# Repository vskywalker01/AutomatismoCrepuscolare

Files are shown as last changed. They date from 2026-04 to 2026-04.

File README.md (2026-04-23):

# Solar-Switcher
This repository contains *source code* and *PCB design* for an automatic load switcher that controls high power consumption devices in base of the energy that a photovoltaic system can currently generate.

## How it works 
The switcher contains four different relays controlled by an Arduino Pro Mini that collects periodically samples from a photo-resistor aligned with the panels and converts them into an estimated power (the power that the inverter should be capable to generate at the time). 
<p align="center">
schematic
</p>

In base of a fixed priority order, the controller turns on and off the relays so that the overall consumptions fits into the estimated power.

## Software 
The software provide a simple user interface controllable by only three buttons (PLUS, MINUS and CONTROL) which contains a general visualization of the relays with dedicated pages for their details and a settings menu, for editing the options in real time. 

> [!NOTE]
> All the settings are automatically saved into the internal EEPROM of the Arduino microcontroller. 

> [!IMPORTANT]
> Currently, only Italian is supported as display language (English support may follow in next updates).

### Sensor conversion and calibration 
The photoresistor used for sampling the light intensity is used for estimating the power that the inverter system can generate on the fly. For this purpose, the analog pin A0 reads constantly the raw values and converts them using a power function defined as 

<h2 align="center">$(\frac{raw - \gamma}{\alpha})^\beta$</h2> 

The three parameters should be tuned by the user in the settings menu in order to assure that the power estimated follows the real one provided by the inverter. 

A good way to do that is to collect known points between *light* value and *power* consumption from the display and tune the parameters on Geogebra so that the curve pass near them. 

<p align="center">

</p>

In my case, for example, knowing that a pump consumes 2kW and a boiler 1.2kW, i obtained that the inverter can handle:
- **pump and boiler** (3,2kW) when the light value is greater or equal to *848*
- **pump until** (2kW) the light value is greater or equal to *800*

### Relay priority system 
The four relays are organined in a fixed priority order where the first one has the highest priority and the last one has the lowest priority. 

Using the power function, the solar switcher tries to turn on the highest amount of relays in order to fit into the estimated power obtained. This means that, as long as a relay with higher priority is turned on, the relays with lower priority will have less available energy. 

> [!NOTE]
> The user can choose to exlude a certain relay from the priority order in the settings using a mask that keeps it deactivated. 

### Source code 
The folder [*software*](software/) folder contains the commented source code of the Solar switcher ready to be flashed to the arduino board. A simple makefile downloads the required libraries, compiles the program and flash the microcontroller automatically using `arduino-cli`:

```
make run PORT=/dev/ttyUSB0 
```

## Hardware 
The folder [*pcb*](pcb/) contains the Kicad project, the [schematic](pcb/pdf/schematic.pdf),the specular [copper layer](pcb/pdf/output.pdf) ready for the press-n-peel and the [silkscreen](pcb/pdf/board.pdf). 

The required components are shown in the following table. 

| Name  | Quantity |
| --- | -- |
| Arduino Pro mini | x1 |
| LCD Display 16x2 | x1 |
| Button | x3 |
| Relay 12 to 24V | x4 |
| 74LS595 | x1 | 
| LM7805 | x1 | 
| BC237 | x4 |
| 1k Ohm resistor | x8 | 
| 10k Ohm resistor | x1 | 
| 510 Ohm resistor | x4 | 
| 10k Ohm trimmer | x1 |
| 2.2k trimmer | x1 | 
| LED | x4 |
| PC817 | x4 | 
| 1N4148 | x4 | 
| 100nf capacitor | x4 | 
| 200mf capacitor | x1 |

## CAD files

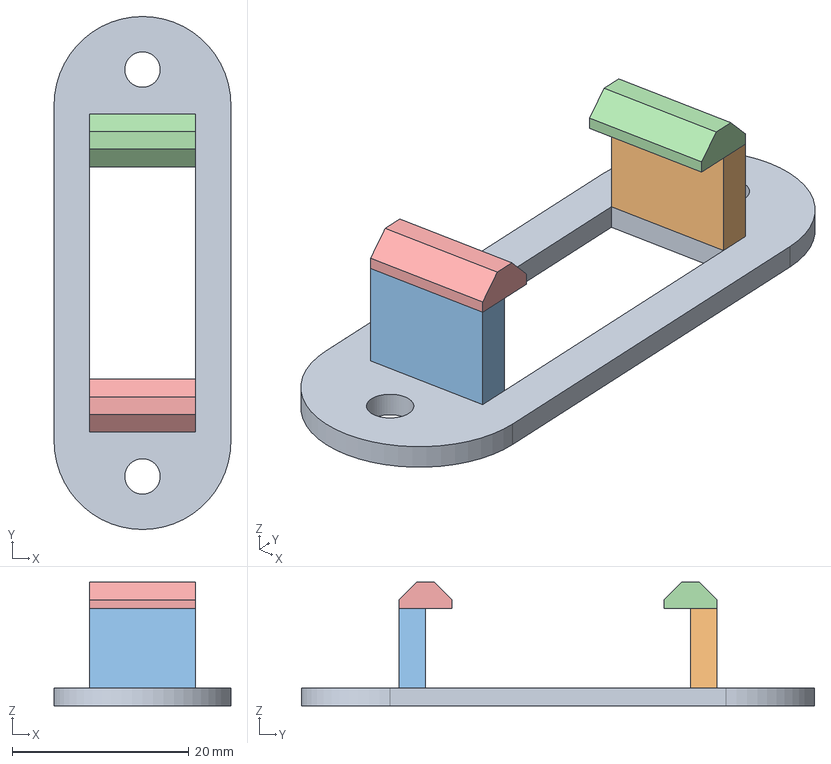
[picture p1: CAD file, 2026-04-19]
3D/button_mask.FCStd
20.0 x 58.0 x 14.0 mm

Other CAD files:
3D/STL/button_mask.stl

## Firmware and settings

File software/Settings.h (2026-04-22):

//Settings class definition 

#ifndef __SETTINGS_H__
#define __SETTINGS_H__

#include "Arduino.h"
#include <EEPROM.h>

/* This class is used for maintaining and storing settings of the program in the EEPROM internal memory. It defines a settings struct and methods to automatically save and load the information. 
 * To check if the data stored in the EEPROM are valid, a simple checksum is estimated and compared with the one stored in the memory. 
*/

#define DEFAULT_POWER       0
#define LOADS_NUMBER        4
#define DEFAULT_TIMEROFF    10
#define DEFAULT_TIMERON     10
#define DEFAULT_BUZZER      true 

#define DEFAULT_ALPHA       966 
#define DEFAULT_BETA        9.6 
#define DEFAULT_GAMMA       0

#define MAX_SETTINGS_BOUND  65536

using namespace std;

//SettingsValues is a struct used for containing the data to save/edit/load 
typedef struct SettingsValues{
    uint32_t checksum;                      //checksum used for verify the data 
    unsigned int powers[LOADS_NUMBER];      //power values for all relays 
    bool masks[LOADS_NUMBER];               //boolean masks for all relays 

    unsigned int defaultTimerOff;           //timer off value 
    unsigned int defaultTimerOn;            //timer on value 

    float alpha;                            //power estimation coefficients. 
    float beta; 
    float gamma;
} SettingsValues;

class Settings {
    private: 
    SettingsValues values;
    public:
    Settings();
    
    //loadDefault() loads default value sin the settings struct 
    void loadDefault();

    //load saved() loads the struct data from the given memory address and check if they are valid:
    //  address -> EEPROM addess of the saved data 
    //returns true if the loaded data is valid or false otherwise (default data is automatically loaded)
    //
    bool loadSaved(unsigned int address);
    
    //store() estimates the checksum and saved the fata from the settings struct to the given memory address 
    //  address -> EEPROM address where store the data 
    void store(unsigned int address);

    //Setter pf the various settings
    void setPower(unsigned int load, unsigned int value);
    void setTimerOn(unsigned int value);
    void setTimerOff(unsigned int value);
    void setMask(unsigned int load, bool value);
    void setAlpha(float alpha);
    void setBeta(float beta);
    void setGamma(float gamma);

    //getters of the various settings 
    float getAlpha();
    float getBeta();
    float getGamma();
    unsigned int getPower(unsigned int load);
    unsigned int getTimerOn();
    unsigned int getTimerOff();
    bool getMask(unsigned int load);

};


#endif 

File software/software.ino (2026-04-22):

// Implementation of main program 

#include "Display.h"
#include "Settings.h"
#include "Sensor.h"
#include "Relays.h"

#include <TimerOne.h>

/*
-- Overview --
An inverter with some photovoltaic panels is connected with two devices: an electic pump and a boiler. The goal is to create a system that, 
in base of the power that the system can generate from the sun, turns on and off the two devices.
Because cloud can create temporary shades on the panels, the system should also not consider occlusions for short amount of times (like 10 minutes). Therefore, a timer should be setted in order to activate or deactivate the relays. 

-- Hardware used --
- An arduino pro mini 
- one 16x2 LCD Display
- three buttons 
- one photoresistor 
- four relays controlled 

-- User interface --
The program include an interface that gives the user control over the settings and the current status of all four relays:
  - The main menu gives the status of the relays (ON/OFF) with the current power (estimated) that is available to all four devices. 

  *********************
  * luce: xxxx  xxxxw *
  * on  off  off  on  *
  *********************

  - A settings menu gives the user control over multipe features like the power used by the loads, output masks, or activation/deactivatiopn timers. 
  
  *********************
  * timer attivazione *
  * > 12s             *
  *********************

  - A details menu gives more information about the current status of each single relay 

  **********************
  * carico 1           *
  * attivazione in xxs *
  **********************

-- relay control system -- 
The four relays have a fixed priority order (relay 1 has the highest priority and relay 4 the least). The system activates first the relays with highest priority and, if th epower is enough for the others, the ones with lowest priority.  

-- light estimation -- 
The estimation of the available power is performes using an exponential model (see Sensor.h)
*/


// ------ DEFINITIONS  ------

//pins connected to the display (see Display.h)
#define LCD_SHIFT_EN              4 
#define LCD_SHIFT_D7              5
#define LCD_SHIFT_SER             6
#define LCD_SHIFT_CLK             7

//display format 
#define LCD_FORMAT_ROWS           2
#define LCD_FORMAT_COLS           20
#define LCD_MAX_COLS              38

//settings EEPROM base address
#define SETTINGS_ADDRESS          0x00

//Sensor pin and constants 
#define PHOTO_PIN                 A0
#define SENSOR_ALPHA_DELTA        1
#define SENSOR_BETA_DELTA         0.1
#define SENSOR_GAMMA_DELTA        1
#define POWER_DELTA               10
//Button pins 
#define SELECT_BUTTON             2
#define MINUS_BUTTON              8
#define PLUS_BUTTON               9

//Relay pins 
#define RELAY1_PIN                1
#define RELAY2_PIN                0
#define RELAY3_PIN                11  
#define RELAY4_PIN                10

//Interface options (values are in microseconds) 
#define DISPLAY_REFRESH_RATE      100000
#define BUTTON_RESOLUTION         2000000
#define BUTTON_FAST_RESOLUTION    100000

//button status enum 
typedef enum {
  CONTROL,
  MINUS,
  PLUS,
  NONE
} button;

//current view enum 
typedef enum {
  GENERAL,
  SETTINGS_POWER,
  SETTINGS_MASK,
  SETTINGS_TIMERON,
  SETTINGS_TIMEROFF,
  SETTINGS_SENSOR
} view;

//global variables  
Display* screen;   //display object 
Settings* options; //settings object 
Sensor* light;     //sensor object 
Relays* counters;  //conters object 

view currentView;                //contains the current menu 
bool blinkStatus;                //used for blinking arrows near the relay status in the main menu 
unsigned int secondCounter;      //used for counting a second from the display interrupts from TimerOne 
unsigned int buttonCounter;      //used for managing the button polling rate 
unsigned short currentSubView;   //sub view used in the menu 
button lastButton;               //last valid button readed  

void update();
void loop() {}

void setup() {
  noInterrupts(); 

  //Pin mode init 
  pinMode(SELECT_BUTTON, INPUT);
  pinMode(MINUS_BUTTON, INPUT);
  pinMode(PLUS_BUTTON, INPUT);
  pinMode(PHOTO_PIN, INPUT);
  pinMode(RELAY1_PIN, OUTPUT);
  pinMode(RELAY2_PIN, OUTPUT);
  pinMode(RELAY3_PIN, OUTPUT);
  pinMode(RELAY4_PIN, OUTPUT);

  //first deactivation of the relays 
  digitalWrite(RELAY1_PIN, true);
  digitalWrite(RELAY2_PIN, true);
  digitalWrite(RELAY3_PIN, true);
  digitalWrite(RELAY4_PIN, true);
  lastButton=NONE;
  currentView=GENERAL;
  blinkStatus=false;

  //the second counter is setted to match exactly one second in base of the display interrupts 
  secondCounter=1000000/DISPLAY_REFRESH_RATE;
  buttonCounter=BUTTON_RESOLUTION/DISPLAY_REFRESH_RATE;

  screen=new Display(LCD_SHIFT_EN, LCD_SHIFT_D7, LCD_SHIFT_SER, LCD_SHIFT_CLK,LCD_FORMAT_ROWS,LCD_FORMAT_COLS,LCD_MAX_COLS);
  options=new Settings();
  counters=new Relays(4);
  
  if(!options->loadSaved(SETTINGS_ADDRESS)) {
    //If the settings saved in the EEPROM are not valid, prints an error on the display 
    screen->clear();
    screen->write(0,0,"Impostazioni non");
    screen->write(1,0,"valide");
    screen->update();
    interrupts();
    delay(2000);
    noInterrupts();
    screen->clear();
  }
  light=new Sensor(PHOTO_PIN,options->getAlpha(),options->getBeta(),options->getGamma());
 
  //interrupt intialization (display refresh rate)
  Timer1.initialize((DISPLAY_REFRESH_RATE/2));
  Timer1.attachInterrupt(update);

  interrupts(); 
}

//timerOne interrupt (display refresh and control system)
void update() {
  //gets the current available light 
  light->readSample();
  unsigned int currentPower=light->getCurrentPower();
  unsigned int currentLight=light->getCurrentValue(); 
  //If one second is elapsed, check the counter status for updating the relays, otherwise the second counter is decremented. 
  if (secondCounter>0) {
    secondCounter--;
  } else {
    //secondCounter reset 
    secondCounter=1000000/DISPLAY_REFRESH_RATE;
    
    //blink arrow update and counter step 
    blinkStatus=!blinkStatus;
    counters->updateStatus();

    //the currentPower value is substracted with the power of the loads to estimate which relay should be modified 
    //(the priority is managed by modifying the leftPowr variable before considering the next relay)
    int leftPower=currentPower;
    for (int l=0;l<LOADS_NUMBER;l++) {
      //if the relay is not masked, leftPower is substracted with the power used by the load
      if (!options->getMask(l)) {
         
        switch (counters->getDirection(l)) {
          case STOP:
            //if relay is turning off but there is enough light -> the relay is maintained on 
            if (leftPower >= options->getPower(l)) {
              leftPower-=options->getPower(l);
              counters->setCount(l,0,ON);
            }
          break;
          case START:
            //if the relay is turning on but there is not enough light -> the relay is maintained off 
            if (leftPower < options->getPower(l)) counters->setCount(l,0,OFF);
          break;
          case ON:
            //if the relay is on but there is not enough light -> the relay counter is started to deactivate the relay 
            if (leftPower < options->getPower(l)) counters->setCount(l,options->getTimerOff(),STOP);
          break;
          case OFF:
            //if the relay is off but there is enough light -> the relay counter is started to activate the relay 
            if (leftPower >= options->getPower(l)) {
              leftPower-=options->getPower(l);
              counters->setCount(l,options->getTimerOn(),START);
            }
          break;
        }
      } else {
        //if the device is masked, its priority is ignored and the relay remains off.
        counters->setCount(l,0,OFF);
      }
      counters->clearFlag(l);
    }
    
    // actual pin update 
    if (counters->getDirection(0)==START || counters->getDirection(0)==OFF) digitalWrite(RELAY1_PIN,true);
    else digitalWrite(RELAY1_PIN,false);
    if (counters->getDirection(1)==START || counters->getDirection(1)==OFF) digitalWrite(RELAY2_PIN,true);
    else digitalWrite(RELAY2_PIN,false);
    if (counters->getDirection(2)==START || counters->getDirection(2)==OFF) digitalWrite(RELAY3_PIN,true);
    else digitalWrite(RELAY3_PIN,false);
    if (counters->getDirection(3)==START || counters->getDirection(3)==OFF) digitalWrite(RELAY4_PIN,true);
    else digitalWrite(RELAY4_PIN,false);

  }

  /* button debouncing system with dynamic resolution */ 

  button detectedButton=NONE;
  button pressedButton=NONE;
  if (!digitalRead(PLUS_BUTTON)) pressedButton=PLUS;
  if (!digitalRead(MINUS_BUTTON)) pressedButton=MINUS;
  if (!digitalRead(SELECT_BUTTON)) pressedButton=CONTROL;
  
  //if the button is pressed and the button counter is off, the button counter is setted. 
  if (buttonCounter==0 || pressedButton != lastButton) {
    //if the last valid button is equal to the pressed one, the polling rate is increased 
    if (lastButton!=pressedButton) buttonCounter=BUTTON_RESOLUTION/DISPLAY_REFRESH_RATE;
    else buttonCounter=BUTTON_FAST_RESOLUTION/DISPLAY_REFRESH_RATE;
    lastButton=pressedButton;
  } else {
    //if the button counter is not zero, the variable is decremented. 
    pressedButton=NONE; 
    buttonCounter--;
  }
  
  /* interface management */ 
  switch (currentView) {
    case GENERAL:
      //If PLUS button is pressed -> go to the next detail page  
      if (pressedButton==PLUS) currentSubView++;

      //If CONTROL button is pressed -> go to the settings page 
      if (pressedButton==CONTROL) {
        if (currentSubView==0) {  
          currentView=SETTINGS_POWER;
        } else {
          //If it is pressed in a detail page -> return to the general view 
          currentSubView=0;
        }
      }
      if (currentSubView==0) {
        //Printing power and light values on the first row 
        screen->write(0,0,"Sole:                ");
        screen->write(0,6,String(currentLight)+"     ");
        screen->write(0,11,String((char) 0b00010000)+" ");
        screen->write(0,13,String(currentPower)+"W   ");

        //Printing relay status on the second row 
        for (unsigned int l=0;l<LOADS_NUMBER ;l++) {
          switch (counters->getDirection(l)) {
            case ON:
              screen->write(1,(l*5),"ON   ");
            break;
            case OFF:
              screen->write(1,(l*5),"OFF  ");
            break;
            case STOP:
              screen->write(1,(l*5),"ON   ");
              if(blinkStatus) {
                screen->write(1,2+(l*5),String((char) 0b00011111));
              } else {
                screen->write(1,2+(l*5),String("  "));
              }
            break;
            case START:
              screen->write(1,(l*5),"OFF  ");
              if(blinkStatus) {
                screen->write(1,3+(l*5),String((char) 0b00011110));
              } else {
                screen->write(1,3+(l*5),String("  "));
              }
            break;
          }
        }

      } else {
        //Details views shows a single relay status. 
        if (currentSubView>LOADS_NUMBER) {
          currentSubView=0;
          currentView=GENERAL;
        } else {

          //Printing the current relay Id and status in the first row and the countdown in the second row (if started) 
          screen->write(0,0,"Porta "+String(currentSubView)+":            ");

          
          switch(counters->getDirection(currentSubView-1)) {
            case ON:
              screen->write(0,10,"ON ");
              screen->write(1,0,"                    ");
              break;
            case STOP:
              screen->write(0,10,"ON ");
              screen->write(1,0,"Spegnimento in "+String(counters->getCount(currentSubView-1))+"    ");
            break;
            
            case OFF:
              screen->write(0,10,"OFF");
              //If the relay is masked, prints "masked in the second row"
              if (options->getMask(currentSubView-1)) {
                screen->write(1,0,"Mascherato          ");
              } else {
                screen->write(1,0,"                    ");
              }
              break;
            case START:
              screen->write(0,10,"OFF");
              screen->write(1,0,"Accensione in "+String(counters->getCount(currentSubView-1))+"    ");
            break;
          }
        }
      }
    break;
    case SETTINGS_MASK:
      //Mask setting view:
      //If the current view = 0 -> the user can select to skip this setting with CONTROL or enter in the menu with PLUS/MINUS 
      //If the current view > 0 -> the user activate the relay's mask with PLUS, deactivate with MINUS or change the view to the next relay ID with CONTROL 
      switch (pressedButton) {
        case PLUS:
          if (currentSubView==0) currentSubView=1;
          else if (currentSubView<=LOADS_NUMBER) options->setMask((currentSubView-1),true);
        break;

        case MINUS:
          if (currentSubView==0) currentSubView=1;
          else if (currentSubView<=LOADS_NUMBER) options->setMask((currentSubView-1),false);
        break;

        case CONTROL:
          if (currentSubView>0) {
            if (currentSubView>=LOADS_NUMBER) {
              currentSubView=0;
              currentView=SETTINGS_SENSOR;
            }
            else {
              currentSubView++;
            }
          } else {
            currentSubView=0;
            currentView=SETTINGS_SENSOR;
          }
        break;
      }
      
      if (currentSubView==0) {
        screen->write(0,0,"Maschere            ");
        screen->write(1,0,"                    ");
      } else {
        screen->write(0,0,"Maschera carico "+String(currentSubView)+"     ");
        screen->write(1,0,String((char) 0b00111110)+"                   ");
        if (options->getMask(currentSubView-1)) {
          screen->write(1,2,String("ON "));
        } else {
          screen->write(1,2,String("OFF "));
        }
        
      }
    break;

    case SETTINGS_POWER:
      //power setting view:
      //If the current view = 0 -> the user can select to skip this setting with CONTROL or enter in the menu with PLUS/MINUS 
      //If the current view > 0 -> the user can adjust the power consumption of the load attached to the relay with PLUS and MINUS or change the view to the next relay ID with CONTROL 

      switch (pressedButton) {
        case PLUS:
          if (currentSubView==0) currentSubView=1;
          else if (currentSubView<=LOADS_NUMBER) options->setPower((currentSubView-1),options->getPower(currentSubView-1)+POWER_DELTA);
        break;

        case MINUS:
          if (currentSubView==0) currentSubView=1;
          else if (currentSubView<=LOADS_NUMBER) options->setPower((currentSubView-1),options->getPower(currentSubView-1)-POWER_DELTA);
        break;

        case CONTROL:
          if (currentSubView>0) {
            if (currentSubView>=LOADS_NUMBER) {
              currentSubView=0;
              currentView=SETTINGS_MASK;
            }
            else {
              currentSubView++;
            }
          } else {
            currentSubView=0;
            currentView=SETTINGS_MASK;
          }
        break;
      }
      if (currentSubView==0) {
        screen->write(0,0,"Potenza carichi     ");
        screen->write(1,0,"                    ");
      } else {
        screen->write(0,0,"Potenza carico "+String(currentSubView)+"     ");
        screen->write(1,0,String((char) 0b00111110)+"                   ");
        screen->write(1,2,String(options->getPower(currentSubView-1))+"    ");
      }
    break;

    //Timer on setting view:
    //the user can adjust the START timer of all relays mask with PLUS and MINUS or change the view to the next setting with CONTROL 

    case SETTINGS_TIMERON:
      switch (pressedButton) {
        case PLUS:
          options->setTimerOn(options->getTimerOn()+1);
        break;

        case MINUS:
          options->setTimerOn(options->getTimerOn()-1);
        break;

        case CONTROL:
          currentView=SETTINGS_TIMEROFF;
        break;
      }
      screen->write(0,0,"Timer allaccio      ");
      screen->write(1,0,String((char) 0b00111110)+"                   ");
      screen->write(1,2,String(options->getTimerOn())+"    ");
    
    break;

    //the user can adjust the STOP timer of all relays mask with PLUS and MINUS or change the view to the next setting with CONTROL
    case SETTINGS_TIMEROFF:
      switch (pressedButton) {
        case PLUS:
          options->setTimerOff(options->getTimerOff()+1);
        break;

        case MINUS:
          options->setTimerOff(options->getTimerOff()-1);
        break;

        case CONTROL:
          screen->clear();
          screen->update();
          currentView=GENERAL;
          currentSubView=0;
          options->store(SETTINGS_ADDRESS);
        break;
      }
      screen->write(0,0,"Timer distacco      ");
      screen->write(1,0,String((char) 0b00111110)+"                   ");
      screen->write(1,2,String(options->getTimerOff())+"    ");
    
    break;
    
    //sensor calibration view:
      //If the current view = 0 -> the user can select to skip this setting with CONTROL or enter in the menu with PLUS/MINUS 
      //If the current view > 0 -> the user can adjust the current coefficient for the sensor power conversion with PLUS and MINUS or change the view to the next one with CONTROL 

    case SETTINGS_SENSOR:
      switch (pressedButton) {
        case PLUS:
          switch (currentSubView) {  
            case 0: 
                currentSubView=1; 
            break; 
            case 1: 
                options->setAlpha(options->getAlpha()+SENSOR_ALPHA_DELTA);
                light->setAlpha(options->getAlpha());
            break;
            case 2: 
                options->setBeta(options->getBeta()+SENSOR_BETA_DELTA);
                light->setBeta(options->getBeta());
            
            case 3: 
                options->setGamma(options->getGamma()+SENSOR_GAMMA_DELTA);
                light->setGamma(options->getGamma());


            default: 
            break;
          }
        break;

        case MINUS:
          switch (currentSubView) {  
            case 0: 
                currentSubView=1; 
            break; 
            case 1: 
                options->setAlpha(options->getAlpha()-SENSOR_ALPHA_DELTA);
                light->setAlpha(options->getAlpha());
            break;
            case 2: 
                options->setBeta(options->getBeta()-SENSOR_BETA_DELTA);
                light->setBeta(options->getBeta());
            
            case 3: 
                options->setGamma(options->getGamma()-SENSOR_GAMMA_DELTA);
                light->setGamma(options->getGamma());

            default: 
            break;
          }  
        break;

        case CONTROL:
          if (currentSubView>0) {
            if (currentSubView>=3) {
              currentSubView=0;
              currentView=SETTINGS_TIMERON;
            }
            else {
              currentSubView++;
            }
          } else {
            currentSubView=0;
            currentView=SETTINGS_TIMERON;
          }
        break;
      }
       
      
      switch (currentSubView) {
        case 0: 
          screen->write(0,0,"Calibrazione sensore");
          screen->write(1,0,"                    ");
        break; 

        case 1:
          screen->write(0,0,"Alpha               ");
          screen->write(1,0,String((char) 0b00111110)+"                   ");
          screen->write(1,2,String(options->getAlpha()));
        break; 

        case 2: 
          screen->write(0,0,"Beta                ");
          screen->write(1,0,String((char) 0b00111110)+"                   ");
          screen->write(1,2,String(options->getBeta()));
        break;
        
        case 3: 
          screen->write(0,0,"Gamma                ");
          screen->write(1,0,String((char) 0b00111110)+"                   ");
          screen->write(1,2,String(options->getGamma()));
        default: 
        break;
      }
    break;

    default:
      currentView=GENERAL;
    break;
  }

  //Sending the text buffer to the display 
  screen->update();
}

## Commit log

2026-03-31 created makefile for arduino-cli
2026-04-19 added 3d model of the button mask and other comments
    [button_mask.FCStd, button_mask.stl]
